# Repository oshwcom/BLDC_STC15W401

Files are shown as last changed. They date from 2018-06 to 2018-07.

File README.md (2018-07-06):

BLDC_STC15W401AS
===========================
一个低成本的12V无刷直流（BLDC）电机的驱动模块。

------

|Author|刘焕银|
|---|---
|E-mail|25199527@qq.com

------

## 目录
* [目标](#目标)
* [功能](#功能)
* [原理图](#原理图)

------

### 目标
    完成一款低成本（人民币7元以下）的BLDC驱动电路。  

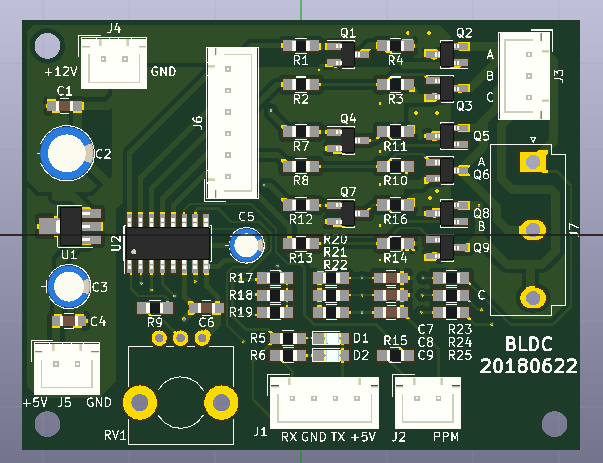
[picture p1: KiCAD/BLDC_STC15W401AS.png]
一款低成本BLDC驱动模块


------

### 功能
1. 驱动12V的BLDC电机，最大输出功率15瓦左右。
2. 可以正反转。
3. 转速800~1500转。

------

### 原理图
    V0.2版原理图。  修订了MOSFET的型号，多加了一种替代封装（SOT23和TO252)。

V0.2版原理图

------

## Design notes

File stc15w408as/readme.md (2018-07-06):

发行记录
===========================
该文件用来记录本次发行的问题

****
	
|Author|刘焕银|
|---|---
|E-mail|25199527@qq.com

已知Bug
------
### PMOS无法关断，换成NMOS后解决
    PMOS始终导通，上臂是12V，烧了大约30个下臂的NMOS。
### MOS管SOA控制不好
    下一版本，更换电流大一点的MOS管。

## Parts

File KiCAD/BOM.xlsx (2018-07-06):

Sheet: Sheet1
Id | 位号 | 封装 | 数量 | 描述
1 | J4 | JST_XH_B02B-XH-A_02x2.50mm_Straight | 1 | DC12V
2 | C1,C4,C6,C7,C8,C9 | C_0805_HandSoldering | 6 | 104
3 | C2 | CP_Radial_D6.3mm_P2.50mm | 1 | 470uF
4 | C3 | CP_Radial_D5.0mm_P2.00mm | 1 | 220uF
5 | C5 | CP_Radial_D4.0mm_P1.50mm | 1 | 47uF
6 | D1,D2 | LED_0805_HandSoldering | 2 | LED
7 | J1 | JST_XH_B04B-XH-A_04x2.50mm_Straight | 1 | Download
8 | J2 | JST_XH_B02B-XH-A_02x2.50mm_Straight | 1 | PPM
9 | J3 | JST_XH_B03B-XH-A_03x2.50mm_Straight | 1 | BLDC
10 | Q1,Q4,Q7 | SOT-23_Handsoldering | 3 | DTC143Z
11 | Q2,Q5,Q8 | SOT-23_Handsoldering | 3 | Q_PMOS_GSD
12 | Q3,Q6,Q9 | SOT-23_Handsoldering | 3 | Q_NMOS_GSD
13 | R1,R5,R6,R7,R12 | R_0805_HandSoldering | 5 | 1k
14 | R2,R8,R13 | R_0805_HandSoldering | 3 | 100
15 | R3,R10,R14 | R_0805_HandSoldering | 3 | 18K
16 | R4,R9,R11,R15,R16 | R_0805_HandSoldering | 5 | 470
17 | R17,R18,R19,R23,R24,R25 | R_0805_HandSoldering | 6 | 10k
18 | R20,R21,R22 | R_0805_HandSoldering | 3 | 2k
19 | RV1 | Potentiometer_Alps_RK09L_Sleve_Single_Horizontal | 1 | RK09L 10K
20 | U1 | SOT-89-3_Handsoldering | 1 | L78L05_SOT89
21 | U2 | SOIC-16_3.9x9.9mm_Pitch1.27mm | 1 | STC15W401AS-SOP16
22 | J5 | JST_XH_B02B-XH-A_02x2.50mm_Straight | 1 | DC5V
23 | J6 | JST_XH_B06B-XH-A_06x2.50mm_Straight | 1 | PWM
24 | J7 | JST_VH_B5P-VH-B_5A3x3.96mm_Vertical | 1 | BLDC

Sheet: Sheet2
Id | 位号 | 封装 | 数量 | 描述 | 单价 | 小计 | 本次数量
1 | J4 | JST_XH_B02B-XH-A_02x2.50mm_Straight | 1 | DC12V |  | 0 | 10
2 | C1,C4,C6,C7,C8,C9 | C_0805_HandSoldering | 6 | 104 |  | 0 | 60
3 | C2 | CP_Radial_D6.3mm_P2.50mm | 1 | 470uF |  | 0 | 10
4 | C3 | CP_Radial_D5.0mm_P2.00mm | 1 | 220uF |  | 0 | 10
5 | C5 | CP_Radial_D4.0mm_P1.50mm | 1 | 47uF |  | 0 | 10
6 | D1,D2 | LED_0805_HandSoldering | 2 | LED |  | 0
7 | J1 | JST_XH_B04B-XH-A_04x2.50mm_Straight | 1 | Download | 0 | 0 | 10
8 | J2 | JST_XH_B02B-XH-A_02x2.50mm_Straight | 1 | PPM | 0 | 0 | 10
9 | J3 | JST_XH_B03B-XH-A_03x2.50mm_Straight | 1 | BLDC | 0 | 0 | 10
10 | Q1,Q4,Q7 | SOT-23_Handsoldering | 3 | DTC143Z | 0.073 | 0.219 | 30
11 | Q2,Q5,Q8 | SOT-23_Handsoldering | 3 | Q_PMOS_GSD | 0.5 | 1.5 | 30
12 | Q3,Q6,Q9 | SOT-23_Handsoldering | 3 | Q_NMOS_GSD | 0.5 | 1.5 | 30
13 | R1,R5,R6,R7,R12 | R_0805_HandSoldering | 5 | 1k | 0.013 | 0.065 | 50
14 | R2,R8,R13 | R_0805_HandSoldering | 3 | 100 | 0.013 | 0.039 | 30
15 | R3,R10,R14 | R_0805_HandSoldering | 3 | 18K | 0.013 | 0.039 | 30
16 | R4,R9,R11,R15,R16 | R_0805_HandSoldering | 5 | 470 | 0.013 | 0.065 | 50
17 | R17,R18,R19,R23,R24,R25 | R_0805_HandSoldering | 6 | 10k | 0.013 | 0.078 | 60
18 | R20,R21,R22 | R_0805_HandSoldering | 3 | 2k | 0.013 | 0.039 | 30
19 | RV1 | Potentiometer_Alps_RK09L_Sleve_Single_Horizontal | 1 | RK09L 10K | 0 | 0 | 10
20 | U1 | SOT-89-3_Handsoldering | 1 | L78L05_SOT89 | 0.25 | 0.25 | 10
21 | U2 | SOIC-16_3.9x9.9mm_Pitch1.27mm | 1 | STC15W401AS-SOP16 | 2.2 | 2.2 | 10
22 | J5 | JST_XH_B02B-XH-A_02x2.50mm_Straight | 1 | DC5V | 0 | 0 | 10
23 | J6 | JST_XH_B06B-XH-A_06x2.50mm_Straight | 1 | PWM | 0 | 0 | 10
24 | J7 | JST_VH_B5P-VH-B_5A3x3.96mm_Vertical | 1 | BLDC | 0 | 0 | 10
 | PCB |  | 1 |  | 1.625 | 1.625 | 10
 | 制造包装测试费用 |  | 1 |  | 1.72 | 1.72
 |  |  |  |  | 总计： | 9.339
 | 电源，12V 3A | https://detail.1688.com/offer/565595260512.html?spm=a360q.7751291.0.0.579e3138QW1meo | 1 |  | 6.8 | 6.8
 | 电机， | https://detail.1688.com/offer/43696222362.html?spm=a360q.8274423.1130995625.41.49c84c9a2D6dGv | 1 |  | 13 | 13

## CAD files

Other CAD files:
stc15w408as/list/main-V20.obj
stc15w408as/comm.OBJ
doc/STC/STC15W401AS-实现四轴飞行器无刷电机的电调控制-参考程序和电路/list/main-V20.obj

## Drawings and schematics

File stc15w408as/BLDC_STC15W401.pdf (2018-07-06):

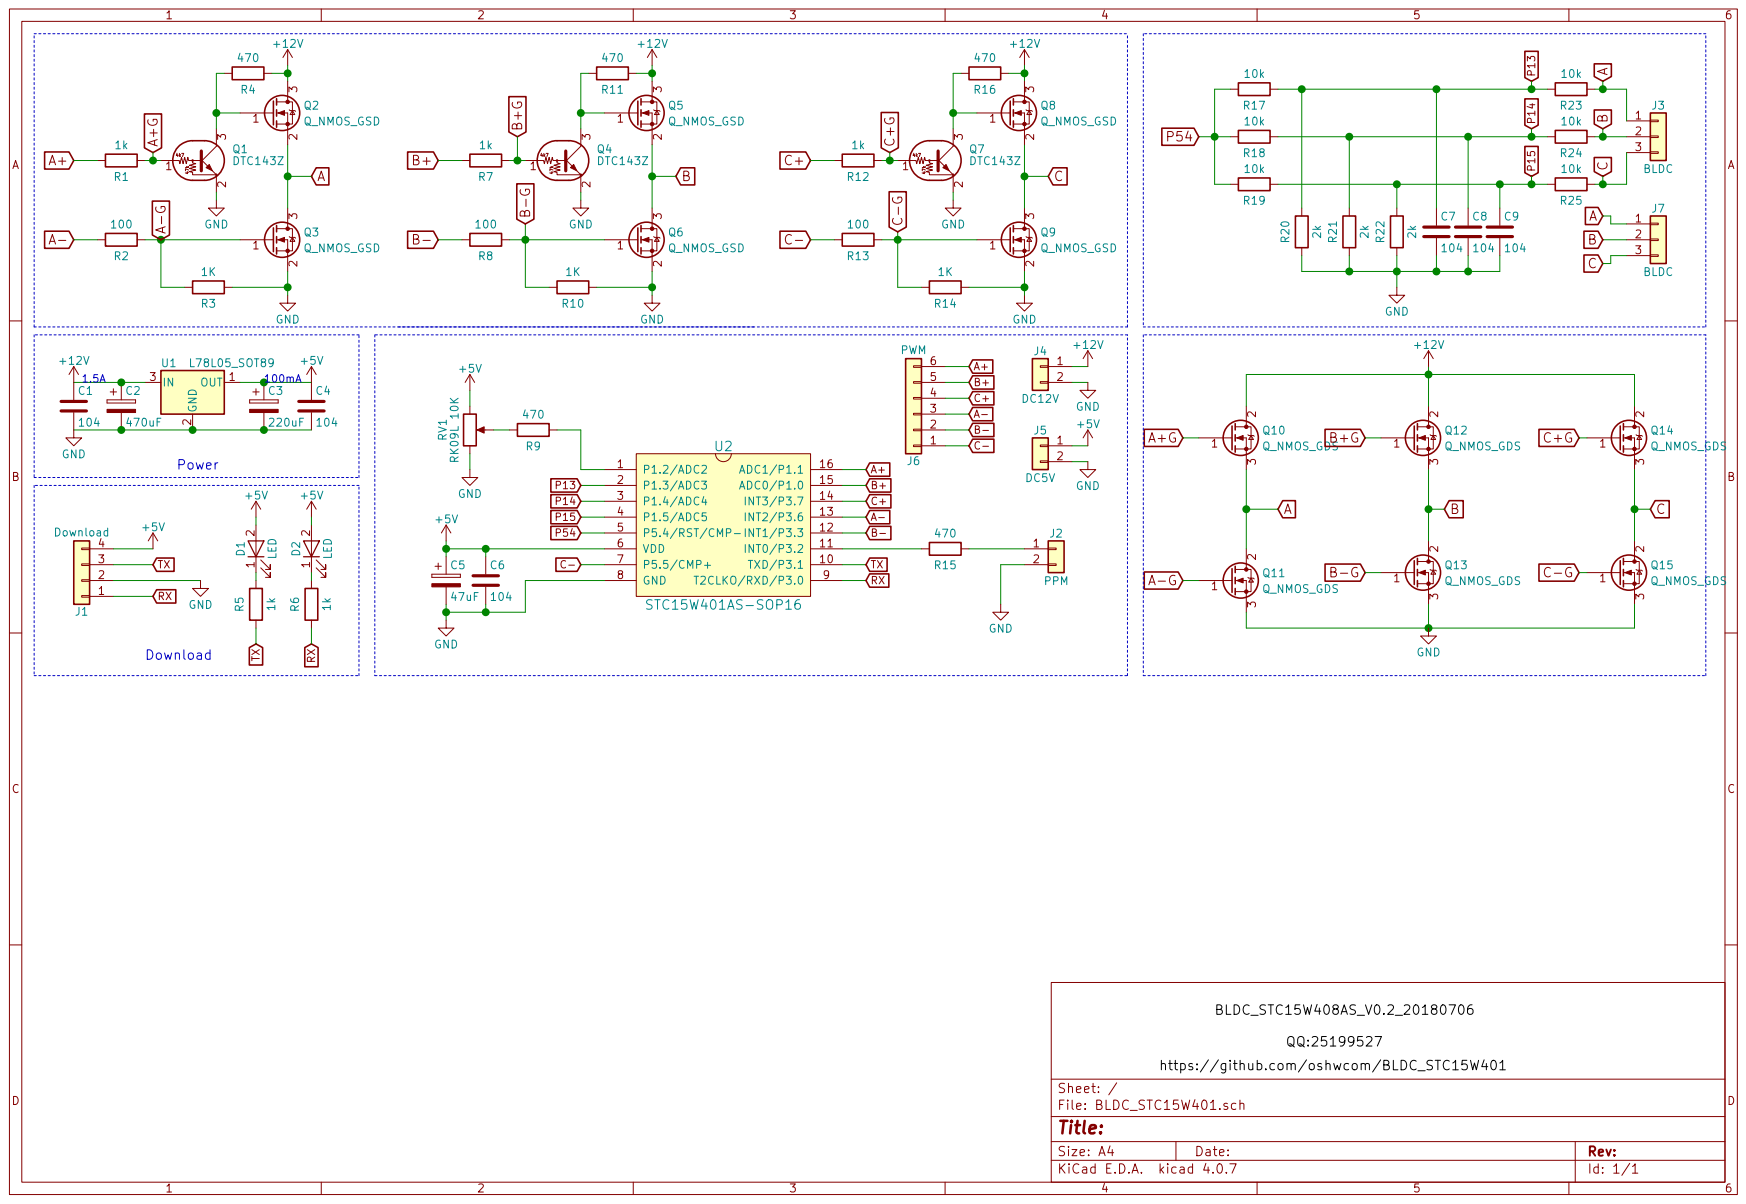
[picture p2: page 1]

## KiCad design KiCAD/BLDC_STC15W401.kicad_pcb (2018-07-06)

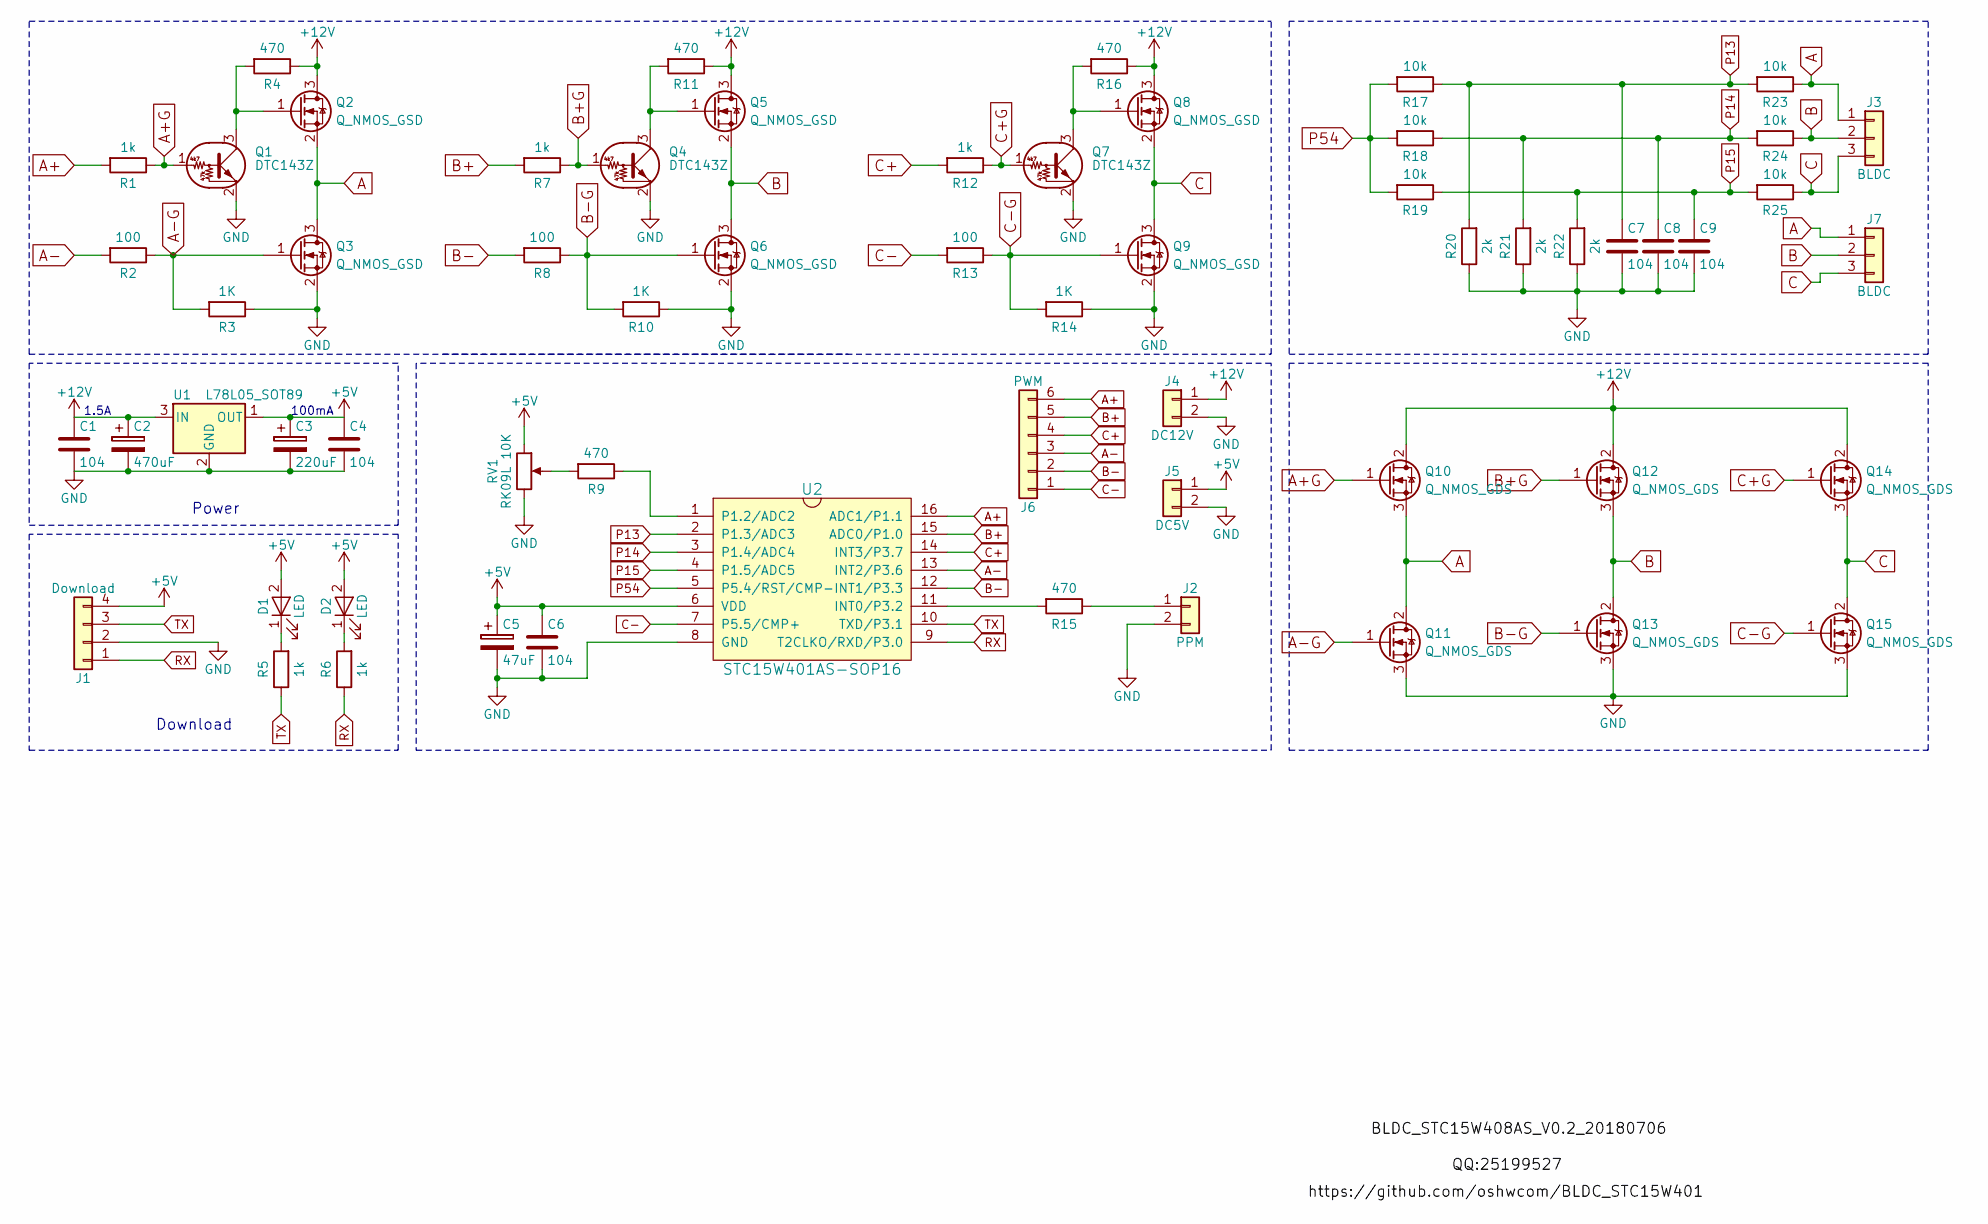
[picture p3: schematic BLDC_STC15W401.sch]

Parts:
C1, C4, C6, C7, C8, C9: 104; C_0805_HandSoldering
C2: 470uF; CP_Radial_D6.3mm_P2.50mm
C3: 220uF; CP_Radial_D5.0mm_P2.00mm
C5: 47uF; CP_Radial_D4.0mm_P1.50mm
D1, D2: LED; LED_0805_HandSoldering
J1: Download; JST_XH_B04B-XH-A_04x2.50mm_Straight
J2: PPM; JST_XH_B02B-XH-A_02x2.50mm_Straight
J3: BLDC; JST_XH_B03B-XH-A_03x2.50mm_Straight
J4: DC12V; JST_XH_B02B-XH-A_02x2.50mm_Straight
J5: DC5V; JST_XH_B02B-XH-A_02x2.50mm_Straight
J6: PWM; JST_XH_B06B-XH-A_06x2.50mm_Straight
J7: BLDC; JST_VH_B5P-VH-B_5A3x3.96mm_Vertical
Q1, Q4, Q7: DTC143Z; SOT-23_Handsoldering
Q2, Q3, Q5, Q6, Q8, Q9: Q_NMOS_GSD; SOT-23_Handsoldering
Q10, Q11, Q12, Q13, Q14, Q15: Q_NMOS_GDS; TO-252-2
R1, R5, R6, R7, R12: 1k; R_0805_HandSoldering
R2, R8, R13: 100; R_0805_HandSoldering
R3, R10, R14: 1K; R_0805_HandSoldering
R4, R9, R11, R15, R16: 470; R_0805_HandSoldering
R17, R18, R19, R23, R24, R25: 10k; R_0805_HandSoldering
R20, R21, R22: 2k; R_0805_HandSoldering
RV1: RK09L 10K; Potentiometer_Alps_RK09L_Sleve_Single_Horizontal
U1: L78L05_SOT89; SOT-89-3_Handsoldering
U2: STC15W401AS-SOP16; SOIC-16_3.9x9.9mm_Pitch1.27mm

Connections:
+5V: C3.1, C4.1, C5.1, C6.1, D1.2 (A), D2.2 (A), J1.4, J5.1, RV1.1, U1.1 (OUT), U2.6 (VDD)
+12V: C1.1, C2.1, J4.1, Q2.3 (D), Q5.3 (D), Q8.3 (D), Q10.2 (D), Q12.2 (D), Q14.2 (D), R4.1, R11.1, R16.1, U1.3 (IN)
A: J3.1, J7.1, Q2.2 (S), Q3.3 (D), Q10.3 (S), Q11.2 (D), R23.1
A+: J6.6, R1.2, U2.16 (ADC1/P1.1)
A+G: Q1.1 (B), Q10.1 (G), R1.1
A-: J6.3, R2.2, U2.13 (INT2/P3.6)
A-G: Q3.1 (G), Q11.1 (G), R2.1, R3.2
B: J3.2, J7.2, Q5.2 (S), Q6.3 (D), Q12.3 (S), Q13.2 (D), R24.1
B+: J6.5, R7.2, U2.15 (ADC0/P1.0)
B+G: Q4.1 (B), Q12.1 (G), R7.1
B-: J6.2, R8.2, U2.12 (INT1/P3.3)
B-G: Q6.1 (G), Q13.1 (G), R8.1, R10.2
C: J3.3, J7.3, Q8.2 (S), Q9.3 (D), Q14.3 (S), Q15.2 (D), R25.1
C+: J6.4, R12.2, U2.14 (INT3/P3.7)
C+G: Q7.1 (B), Q14.1 (G), R12.1
C-: J6.1, R13.2, U2.7 (P5.5/CMP+)
C-G: Q9.1 (G), Q15.1 (G), R13.1, R14.2
GND: C1.2, C2.2, C3.2, C4.2, C5.2, C6.2, C7.2, C8.2, C9.2, J1.2, J2.2, J4.2, J5.2, Q1.2 (E), Q3.2 (S), Q4.2 (E), Q6.2 (S), Q7.2 (E), Q9.2 (S), Q11.3 (S), Q13.3 (S), Q15.3 (S), R3.1, R10.1, R14.1, R20.1, R21.1, R22.1, RV1.3, U1.2 (GND), U2.8 (GND)
unnamed: D1.1 (K), R5.2
unnamed: D2.1 (K), R6.2
unnamed: J2.1, R15.1
unnamed: Q1.3 (C), Q2.1 (G), R4.2
unnamed: Q4.3 (C), Q5.1 (G), R11.2
unnamed: Q7.3 (C), Q8.1 (G), R16.2
unnamed: R9.1, U2.1 (P1.2/ADC2)
unnamed: R9.2, RV1.2
unnamed: R15.2, U2.11 (INT0/P3.2)
P13: C7.1, R17.1, R20.2, R23.2, U2.2 (P1.3/ADC3)
P14: C8.1, R18.1, R21.2, R24.2, U2.3 (P1.4/ADC4)
P15: C9.1, R19.1, R22.2, R25.2, U2.4 (P1.5/ADC5)
P54: R17.2, R18.2, R19.2, U2.5 (P5.4/RST/CMP-)
RX: J1.1, R6.1, U2.9 (T2CLKO/RXD/P3.0)
TX: J1.3, R5.1, U2.10 (TXD/P3.1)

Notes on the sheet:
Power
Download
100mA
1.5A

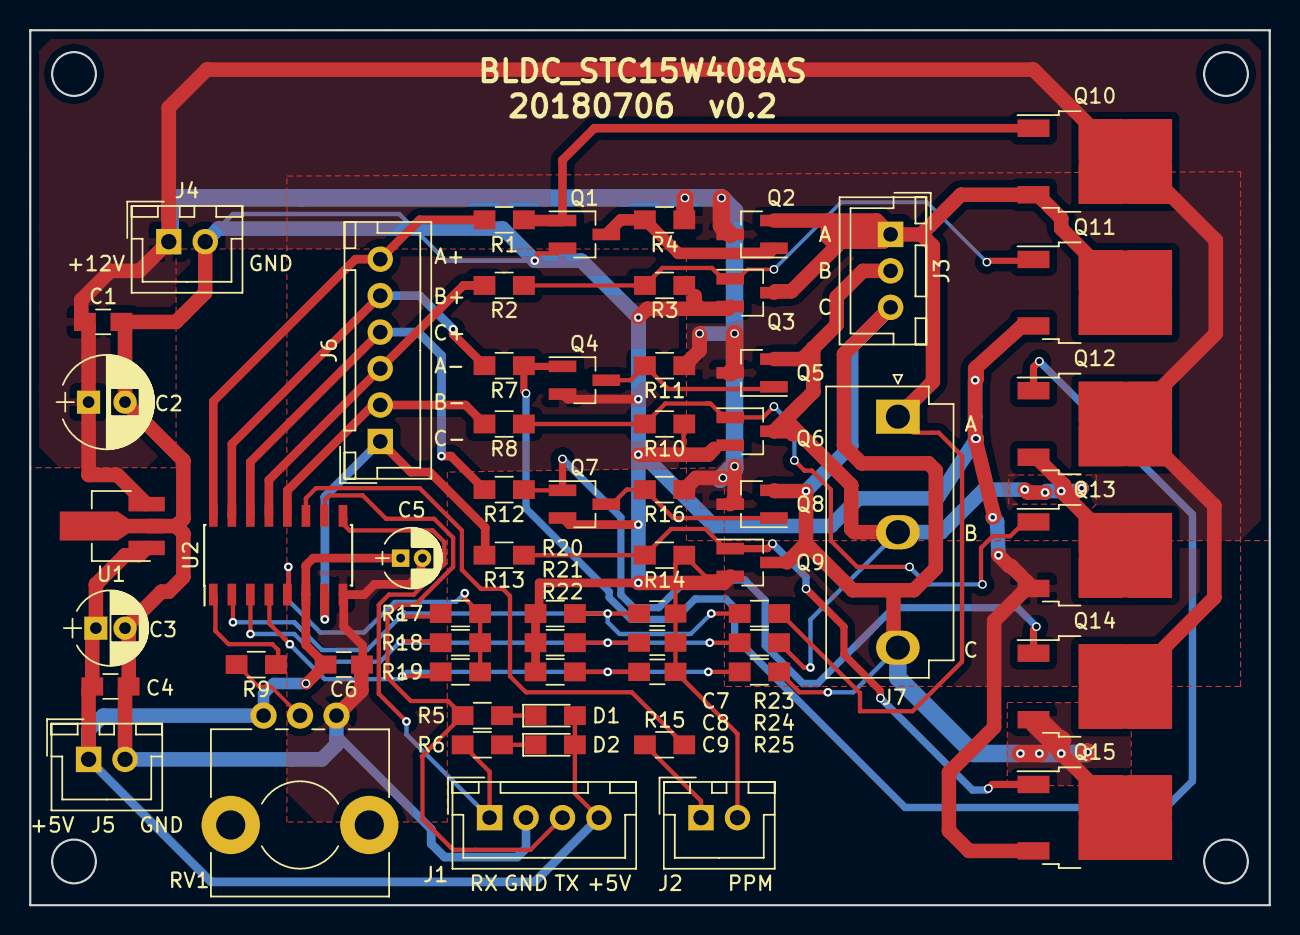
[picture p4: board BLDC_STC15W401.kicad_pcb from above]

Board: 2 copper layers, 85.0 x 60.0 mm, 61 parts (0 on the bottom side), 33 nets.

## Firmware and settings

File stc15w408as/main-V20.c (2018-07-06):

/*---------------------------------------------------------------------*/
/* --- STC MCU International Limited ----------------------------------*/
/* --- STC 1T Series MCU Demo Programme -------------------------------*/
/* --- Mobile: 13922805190 --------------------------------------------*/
/* --- Fax: 0513-55012956,55012947,55012969 ---------------------------*/
/* --- Tel: 0513-55012928,55012929,55012966 ---------------------------*/
/* --- Web: www.GXWMCU.com   www.stcmcu.com ---------------------------*/
/* --- QQ:  800003751 -------------------------------------------------*/
/* 如果要在程序中使用此代码,请在程序中注明使用了宏晶科技的资料及程序   */
/*---------------------------------------------------------------------*/


/*************	功能说明	**************

本程序试验使用STC15W401AS-35I-SOP16<RMB1.6>来驱动航模用的无传感器无刷三相直流马达.

本程序参考自网上的代码(作者: 瑞生), 改良而来.

电路图见文件 "BLDC-V10-实验电路.pdf".

控制信号由P3.2输入正脉冲信号, 间隔5~20ms, 脉冲宽度1.000~1.610ms.

1.160ms开始启动, 1.610ms为最高速度, 分辨率为2us.

本程序仅仅是简单控制, 软件没有处理 过0延时30度切换 过流检测.

由于过0检测部分有RC滤波, 所以改变电容值可以大约的对应在最高速时延时30度的时间.

有意者可自行完善电路和程序.

******************************************/




#define MAIN_Fosc		24000000L	//定义主时钟

#include "STC15Fxxxx.H"

#define		MCU_PIN		16	/* 选择MCU引脚数, 只支持16或20脚(28脚或32脚跟20脚一样) */

// #include "reg51.h"
#include "intrins.h"

typedef unsigned char BYTE;
typedef unsigned int WORD;
void SendData(BYTE dat);
void SendString(char *s);
// #define FOSC 11059200L          //系统频率
// #define BAUD 115200             //串口波特率

#define NONE_PARITY     0       //无校验
#define ODD_PARITY      1       //奇校验
#define EVEN_PARITY     2       //偶校验
#define MARK_PARITY     3       //标记校验
#define SPACE_PARITY    4       //空白校验

#define PARITYBIT NONE_PARITY   //定义校验位



//CMPCR1
#define	CMPEN	0x80	//1: 允许比较器, 0: 禁止,关闭比较器电源
#define	CMPIF	0x40	//比较器中断标志, 包括上升沿或下降沿中断, 软件清0
#define	PIE		0x20	//1: 比较结果由0变1, 产生上升沿中断
#define	NIE		0x10	//1: 比较结果由1变0, 产生下降沿中断
#define	PIS		0x08	//输入正极性选择, 0: 选择外部P5.5做正输入,           1: 由ADCIS[2:0]所选择的ADC输入端做正输入.
#define	NIS		0x04	//输入负极性选择, 0: 选择内部BandGap电压BGv做负输入, 1: 选择外部P5.4做输入.
#define	CMPOE	0x02	//1: 允许比较结果输出到P1.2, 0: 禁止.
#define	CMPRES	0x01	//比较结果, 1: CMP+电平高于CMP-,  0: CMP+电平低于CMP-,  只读

//CMPCR2
#define	INVCMPO	0x80	//1: 比较器输出取反,  0: 不取反
#define	DISFLT	0x40	//1: 关闭0.1uF滤波,   0: 允许
#define	LCDTY	0x00	//0~63, 比较结果变化延时周期数

#if	(MCU_PIN == 20)
	sbit PWM2_L = P3^4;
	sbit PWM1_L = P3^5;
	sbit PWM0_L = P3^6;
#endif

#if	(MCU_PIN == 16)
	sbit PWM2_L = P5^5;		// C-
	sbit PWM1_L = P3^3;		// B-
	sbit PWM0_L = P3^6;		// A-
#endif

u8	Step;
u8	PWM_Value; // 决定PWM占空比的值
u16	RxPulseWide;
bit	B_RxOk;
bit	B_RUN;
u8	PWW_Set;
u8	cnt10ms;
u8	Rx_cnt;
u8	TimeOut;	//堵转超时

#define DISABLE_CMP_INT CMPCR1 &= ~0X40		// 关闭比较器中断
#define ENABLE_CMP_INT  CMPCR1 |= 0X40		// 打开比较器中断

/*************************/

void	Delay_n_ms(u8 dly)
{
	u16	j;
	do
	{
		j = MAIN_Fosc / 13000;	//延时1ms, 主程序在此节拍下运行
		while(--j)	;
	}while(--dly);
}


void delay_us(u8 us)
{
	do
	{
		NOP(20);	//@24MHz
	}
	while(--us);
}

void StepXL(void) // 换相序列函数
{
 switch(Step)
  {
   case 0:  // AB
			PWM0_L=0;	PWM2_L=0;
			PWM0_OUT_1();
			PWM1_OUT_1();
			PWM2_OUT_1();
			PWM0_NORMAL();
			CCAP0H = PWM_Value;		// 打开A相的高端
			PWM1_L = 1; 		// 打开B相的低端
			ADC_CONTR = 0XED;	// 选择P1.5作为ADC输入 即c相电压
			CMPCR1 = 0x9C;		//bit7=1 允许比较器, bit4=1 比较结果由1变0, 产生下降沿中断 (不能响应下降沿中断?)
		break;
   case 1:  // AC
			PWM0_L=0;	PWM1_L=0;
			PWM0_OUT_1();
			PWM1_OUT_1();
			PWM2_OUT_1();
			PWM0_NORMAL();
			CCAP0H = PWM_Value;		// 打开A相的高端
			PWM2_L = 1;			// 打开C相的低端
			ADC_CONTR = 0XEC;	// 选择P1.4作为ADC输入 即B相电压
			CMPCR1 = 0xAC;		//上升沿中断
	 
      	break;
   case 2:  // BC
			PWM0_L=0;	PWM1_L=0;
			PWM0_OUT_1();
			PWM1_OUT_1();
			PWM2_OUT_1();
			PWM1_NORMAL();
			CCAP1H = PWM_Value; // 打开B相的高端
			PWM2_L = 1;			// 打开C相的低端
			ADC_CONTR = 0XEB;	// 选择P1.3作为ADC输入 即a相电压
			CMPCR1 = 0x9C;		//下降沿中断
      	break;
   case 3:  // BA
			PWM1_L=0;	PWM2_L=0;
			PWM0_OUT_1();
			PWM1_OUT_1();
			PWM2_OUT_1();
			PWM1_NORMAL();
			CCAP1H = PWM_Value; // 打开B相的高端
			PWM0_L = 1;			// 打开A相的低端
			ADC_CONTR = 0XED;	// 选择P1.5作为ADC输入 即c相电压 
			CMPCR1 = 0xAC;		//上升沿中断
			
      	break;
   case 4: // CA
			PWM1_L=0;	PWM2_L=0;
			PWM0_OUT_1();
			PWM1_OUT_1();
			PWM2_OUT_1();
			PWM2_NORMAL();
			CCAP2H = PWM_Value; // 打开C相的高端
			PWM0_L = 1;			// 打开A相的低端
			ADC_CONTR = 0XEC;	// 选择P1.4作为ADC输入 即B相电压
			CMPCR1 = 0x9C;		//下降沿中断
     	break;
   case 5: // CB
      		PWM0_L=0;	PWM2_L=0;
			PWM0_OUT_1();
			PWM1_OUT_1();
			PWM2_OUT_1();
			PWM2_NORMAL();
			CCAP2H = PWM_Value; // 打开C相的高端
      		PWM1_L = 1;			// 打开B相的低端
			ADC_CONTR = 0XEB;	// 选择P1.3作为ADC输入 即a相电压
			CMPCR1 = 0xAC;		//上升沿中断
	 
		break;
	 
	default:
		break;
  }	
}



void PWM_Init(void)
{
	PWM0_L = 0;
	PWM1_L = 0;
	PWM2_L = 0;
	
	#if	(MCU_PIN == 20)
		P3n_push_pull(0x70);
	#endif
	#if	(MCU_PIN == 16)
		P3n_push_pull(0x48);
		P5n_push_pull(0x20);
	#endif

	// CMOD = 1 << 1; //选择系统时钟/2为时钟源，即PWM频率=24M/2/256=46.9K
	CMOD = 5 << 1; //选择系统时钟/4为时钟源，即PWM频率=24M/4/256=23.4K
	// CMOD = 6 << 1; //选择系统时钟/6为时钟源，即PWM频率=24M/6/256=15.6K
	CL=0;			// PCA计数器清零
	CH=0;
	
	PCA_PWM0 = 0X00;
	CCAP0H=0;    // 初始化占空比为0% H的值装载到L中
	CCAP0L=0;
	CCAPM0=0x42;	// 设置为PWM模式, 8位，无中断。

	PCA_PWM1 = 0X00;
	CCAP1H=0;    // 初始化占空比为0%
	CCAP1L=0;
	CCAPM1=0x42;	// 设置为PWM模式
	
	PCA_PWM2 = 0X00;
	CCAP2H=0;    // 初始化占空比为0%
	CCAP2L=0;
	CCAPM2=0x42;	// 设置为PWM模式
	
	PWM0_OUT_1();
	PWM1_OUT_1();
	PWM2_OUT_1();

	CR = 1;
}

void ADC_Init(void)
{
	P1n_pure_input(0x38);
	P1ASF = 0X38; // 开通P1.3 P1.4 P1.5的AD输入口
}

void CMP_INT(void) interrupt 21
{
	CMPCR1 &= ~0X40; // 需软件清除中断标志位
	if(Step<5)	Step++;
	else		Step = 0;
	StepXL();
	TimeOut = 10;	//10ms超时
}

void CMP_Init(void)
{
	CMPCR1 = 0X8C;	// 1000 1100 打开比较器，P5.4作为比较器的反相输入端，ADC引脚作为正输入端 
	CMPCR2 = 60;	// 60个时钟滤波
	P5n_pure_input(0x10);
}

u8 StartMotor(void)
{
	u16 timer,i;
	DISABLE_CMP_INT;	// 禁止比较器中断
	PWM_Value = 30;		// 初始占空比=16/256=6%
	Step = 0;
	StepXL();			// 初始位置
	Delay_n_ms(5);//delay_ms(5);
	timer = 300;

	while(1)
	{
		for(i=0; i<timer; i++)	delay_us(50);  // 第一次是15毫秒，加上上面的5毫米延时，总计大约20毫秒
		timer -= timer /15 + 1;
		if(timer < 25)	{
			CMPCR1 &= ~0X40; 	// 需软件清除中断标志位
			B_RUN = 1;			// 马达运行标志位
			PWM_Value = 0;		// 启动完成。停转，等串口的PWW_SET值
			TimeOut = 10;		// 10毫米超时
			ENABLE_CMP_INT; 	// 打开比较器中断
			return(1);
		}
		if( Step < 5)	Step++;
		else			Step = 0;
		StepXL();
		// SendString("Start Motor!\r\n");
	}
}

// void T0_Iint(void)
// {
// 	Timer0_AsTimer();	/* 时器0用做定时器	*/
// 	Timer0_12T();		/* Timer0 clodk = fo/12	12分频,	default	*/
// 	Timer0_16bit();
// 	Timer0_Gate_INT0_P32();	/* 时器0由外部INT0高电平允许定时计数 */
// 	TH0 = 0;
// 	TL0 = 0;
// 	TR0 = 1; // 打开定时器0
// 	ET0 = 1;// 允许ET0中断
// }

// void T0_Interrupt(void) interrupt 1
// {
// 	Rx_cnt = 0;			//一旦出现溢出, 则开始的n个脉冲无效
// 	RxPulseWide = 1000;	//停止
// 	B_RxOk = 1;			//虚拟收到一个脉冲
// }

/********************* INT0中断函数 *************************/
// void INT0_int (void) interrupt INT0_VECTOR
// {
// 	u16	j;
	
// 	TR0 = 0;
// 	j = ((u16)TH0 << 8) + TL0;
// 	TH0 = 0;
// 	TL0 = 0;
// 	TR0 = 1;

// 	if(++Rx_cnt >= 5)	Rx_cnt = 5;
// 	j >>= 1;	//为了好处理, 转成单位为us
// 	if((j >= 800) && (j <= 2000) && (Rx_cnt == 5))
// 	{
// 		RxPulseWide = j;
// 		B_RxOk = 1;		//标志收到一个脉冲
// 	}

// }

/********************* 串口初始化函数 *************************/
bit busy;


void UartInit(void)		//9600bps@24.000MHz
{
	SCON = 0x50;		//8位数据,可变波特率
	AUXR |= 0x01;		//串口1选择定时器2为波特率发生器
	AUXR |= 0x04;		//定时器2时钟为Fosc,即1T
	T2L = 0x8F;		//设定定时初值
	T2H = 0xFD;		//设定定时初值
	AUXR |= 0x10;		//启动定时器2
    ES = 1;                     //使能串口1中断
}


/*----------------------------
UART 中断服务程序
-----------------------------*/
void Uart() interrupt 4 using 1
{
    ES = 0;         //关闭串口中断
	if (RI)
    {
		PWW_Set = SBUF; // 把收到的数据给了PWW_Set
		RI=0; // 串口接收标志清0
		B_RxOk = 1;
    }
    if (TI)
    {
        TI = 0;                 //清除TI位
        busy = 0;               //清忙标志
    }
	ES = 1;         //使能串口中断
}


/*----------------------------
发送串口数据
----------------------------*/
void SendData(BYTE dat)
{
    while (busy);               //等待前面的数据发送完成
    ACC = dat;                  //获取校验位P (PSW.0)
    if (P)                      //根据P来设置校验位
    {
		#if (PARITYBIT == ODD_PARITY)
				TB8 = 0;                //设置校验位为0
		#elif (PARITYBIT == EVEN_PARITY)
				TB8 = 1;                //设置校验位为1
		#endif
    }
    else
    {
		#if (PARITYBIT == ODD_PARITY)
				TB8 = 1;                //设置校验位为1
		#elif (PARITYBIT == EVEN_PARITY)
				TB8 = 0;                //设置校验位为0
		#endif
    }
    busy = 1;
    SBUF = ACC;                 //写数据到UART数据寄存器
}

/*----------------------------
发送字符串
----------------------------*/
void SendString(char *s)
{
    while (*s)                  //检测字符串结束标志
    {
        SendData(*s++);         //发送当前字符
    }
}


/**********************************************/

void main(void)
{
	PWM_Init();
	ADC_Init();
	CMP_Init();
	UartInit();
	// T0_Iint();

	IE0 = 0;	// 清除外中断0标志位
	// EX0 = 1;	// INT0 Enable
	// IT0 = 1;	//INT0 下降沿中断
	
	// RxPulseWide = 1000;
	PWW_Set = 0;
	cnt10ms = 0;
	Rx_cnt  = 0;
	TimeOut = 0;

	EA = 1; // 打开总中断
	// Delay_n_ms(1);	//延时
	SendString("BLDC Test !\r\n");
	while (1)
	{
		Delay_n_ms(1);	//延时1ms, 主程序在此节拍下运行

		if (TimeOut > 0)
		{
			if(--TimeOut == 0)	//堵转超时
			{
				DISABLE_CMP_INT; 	// 关比较器中断
				CCAP0H=0;	CCAP1H=0;	CCAP2H=0;  // 占空比为0
				PWM0_L=0;	PWM1_L=0;	PWM2_L=0;
				// RxPulseWide = 1000;
				PWW_Set   = 0;
				PWM_Value = 0;
				B_RxOk = 0;
				B_RUN  = 0;
				Rx_cnt = 0;
				TimeOut = 0;
				SendString("Time Out!\r\n");

				Delay_n_ms(250);	//堵转时,延时1秒再启动
				Delay_n_ms(250);
				Delay_n_ms(250);
				Delay_n_ms(250);

			}
		}
		
		// if(B_RxOk)	//收到一个脉冲
		// {
		// 	B_RxOk = 0;
		// 	j = RxPulseWide;
		// 	if(j >= 1100)				// 1100~1610对应PWM占空比值0~255
		// 	{
		// 		j = (j - 1100) >> 1;	//2us对应PWM一个步进
		// 		if(j > 256)	j = 255;
		// 	}
		// 	else	j = 0;
		// 	PWW_Set = (u8)j;
		// }
		// SendData(PWW_Set);
		if(B_RxOk) // 如果串口收到数据
		{
			// SendData(PWW_Set);
			B_RxOk = 0;
			// if(rec==0x22)// 加速命令
			// {
			// 	if(PWM_Value<250)
			// 	{
			// 		PWM_Value++; // 增加占空比
			// 	}
			// }
			// else if(rec==0x33)// 减速命令
			// {
			// 	if(PWM_Value>30)
			// 	{
			// 		PWM_Value--; // 减小占空比
			// 	}
			// }
			// else if(rec==0x11) // 启动命令
			// {
			// 	StartMotor();	// 启动马达
			// 	CMPCR1 &= ~0X40; // 需软件清除中断标志位
			// 	ENABLE_CMP_INT; // 打开比较器中断
			// 	B_RUN = 1;
			// 	TimeOut = 0;
			// }
			// else if(rec==0x44) // 停止命令
			// {
			// 	CCAP0H=0;CCAP1H=0;CCAP2H=0;  // 占空比都置0
			// 	EA = 0; // 关闭全局中断
			// 	DISABLE_CMP_INT; // 关闭比较器中断
			// }
		}
		if(!B_RUN && (PWW_Set >= 30))		// PWM_Set >= 30, 并且马达未运行, 则启动马达
		{
			StartMotor();	// 启动马达
			// TimeOut = 0;
		}
		
		
		if(++cnt10ms >= 10)		// 10ms时隙
		{
			// SendData(cnt10ms);
			cnt10ms = 0;
			if(B_RUN)
			{
				if(PWM_Value < PWW_Set)	PWM_Value++;
				if(PWM_Value > PWW_Set)	PWM_Value--;
				if(PWM_Value < 20)	// 停转
				{
					PWM_Value = 0;
					B_RUN = 0;
					CCAP0H=0;	CCAP1H=0;	CCAP2H=0;  // 占空比为0
					PWM0_L=0;	PWM1_L=0;	PWM2_L=0;
					DISABLE_CMP_INT; // 关比较器中断
					SendString("Stop Motor!\r\n");
				}
			}
		}
	}
}

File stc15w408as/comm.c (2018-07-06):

/*---------------------------------------------------------------------*/
/* --- STC MCU Limited ------------------------------------------------*/
/* --- STC15F4K60S4 系列 定时器2用作串口1的波特率发生器举例------------*/
/* --- Mobile: (86)13922805190 ----------------------------------------*/
/* --- Fax: 86-0513-55012956,55012947,55012969 ------------------------*/
/* --- Tel: 86-0513-55012928,55012929,55012966-------------------------*/
/* --- Web: www.STCMCU.com --------------------------------------------*/
/* --- Web: www.GXWMCU.com --------------------------------------------*/
/* 如果要在程序中使用此代码,请在程序中注明使用了STC的资料及程序        */
/* 如果要在文章中应用此代码,请在文章中注明使用了STC的资料及程序        */
/*---------------------------------------------------------------------*/

//本示例在Keil开发环境下请选择Intel的8058芯片型号进行编译
//若无特别说明,工作频率一般为11.0592MHz


#include "reg51.h"
#include "intrins.h"

typedef unsigned char BYTE;
typedef unsigned int WORD;

#define FOSC 11059200L          //系统频率
#define BAUD 115200             //串口波特率

#define NONE_PARITY     0       //无校验
#define ODD_PARITY      1       //奇校验
#define EVEN_PARITY     2       //偶校验
#define MARK_PARITY     3       //标记校验
#define SPACE_PARITY    4       //空白校验

#define PARITYBIT EVEN_PARITY   //定义校验位

sfr P0M1 = 0x93;
sfr P0M0 = 0x94;
sfr P1M1 = 0x91;
sfr P1M0 = 0x92;
sfr P2M1 = 0x95;
sfr P2M0 = 0x96;
sfr P3M1 = 0xb1;
sfr P3M0 = 0xb2;
sfr P4M1 = 0xb3;
sfr P4M0 = 0xb4;
sfr P5M1 = 0xC9;
sfr P5M0 = 0xCA;
sfr P6M1 = 0xCB;
sfr P6M0 = 0xCC;
sfr P7M1 = 0xE1;
sfr P7M0 = 0xE2;

sfr AUXR  = 0x8e;               //辅助寄存器
sfr T2H   = 0xd6;               //定时器2高8位
sfr T2L   = 0xd7;               //定时器2低8位

sfr P_SW1   = 0xA2;             //外设功能切换寄存器1

#define S1_S0 0x40              //P_SW1.6
#define S1_S1 0x80              //P_SW1.7

sbit P22 = P2^2;

bit busy;

void SendData(BYTE dat);
void SendString(char *s);

void main()
{
    P0M0 = 0x00;
    P0M1 = 0x00;
    P1M0 = 0x00;
    P1M1 = 0x00;
    P2M0 = 0x00;
    P2M1 = 0x00;
    P3M0 = 0x00;
    P3M1 = 0x00;
    P4M0 = 0x00;
    P4M1 = 0x00;
    P5M0 = 0x00;
    P5M1 = 0x00;
    P6M0 = 0x00;
    P6M1 = 0x00;
    P7M0 = 0x00;
    P7M1 = 0x00;

    ACC = P_SW1;
    ACC &= ~(S1_S0 | S1_S1);    //S1_S0=0 S1_S1=0
    P_SW1 = ACC;                //(P3.0/RxD, P3.1/TxD)
    
    //  ACC = P_SW1;
    //  ACC &= ~(S1_S0 | S1_S1);    //S1_S0=1 S1_S1=0
    //  ACC |= S1_S0;               //(P3.6/RxD_2, P3.7/TxD_2)
    //  P_SW1 = ACC;  
    //  
    //  ACC = P_SW1;
    //  ACC &= ~(S1_S0 | S1_S1);    //S1_S0=0 S1_S1=1
    //  ACC |= S1_S1;               //(P1.6/RxD_3, P1.7/TxD_3)
    //  P_SW1 = ACC;  

    #if (PARITYBIT == NONE_PARITY)
        SCON = 0x50;                //8位可变波特率
    #elif (PARITYBIT == ODD_PARITY) || (PARITYBIT == EVEN_PARITY) || (PARITYBIT == MARK_PARITY)
        SCON = 0xda;                //9位可变波特率,校验位初始为1
    #elif (PARITYBIT == SPACE_PARITY)
        SCON = 0xd2;                //9位可变波特率,校验位初始为0
    #endif

    T2L = (65536 - (FOSC/4/BAUD));   //设置波特率重装值
    T2H = (65536 - (FOSC/4/BAUD))>>8;
    AUXR = 0x14;                //T2为1T模式, 并启动定时器2
    AUXR |= 0x01;               //选择定时器2为串口1的波特率发生器
    ES = 1;                     //使能串口1中断
    EA = 1;

    SendString("STC15F2K60S2\r\nUart Test !\r\n");
    while(1);
}

/*----------------------------
UART 中断服务程序
-----------------------------*/
void Uart() interrupt 4 using 1
{
    if (RI)
    {
        RI = 0;                 //清除RI位
        P0 = SBUF;              //P0显示串口数据
        P22 = RB8;              //P2.2显示校验位
    }
    if (TI)
    {
        TI = 0;                 //清除TI位
        busy = 0;               //清忙标志
    }
}

/*----------------------------
发送串口数据
----------------------------*/
void SendData(BYTE dat)
{
    while (busy);               //等待前面的数据发送完成
    ACC = dat;                  //获取校验位P (PSW.0)
    if (P)                      //根据P来设置校验位
    {
#if (PARITYBIT == ODD_PARITY)
        TB8 = 0;                //设置校验位为0
#elif (PARITYBIT == EVEN_PARITY)
        TB8 = 1;                //设置校验位为1
#endif
    }
    else
    {
#if (PARITYBIT == ODD_PARITY)
        TB8 = 1;                //设置校验位为1
#elif (PARITYBIT == EVEN_PARITY)
        TB8 = 0;                //设置校验位为0
#endif
    }
    busy = 1;
    SBUF = ACC;                 //写数据到UART数据寄存器
}

/*----------------------------
发送字符串
----------------------------*/
void SendString(char *s)
{
    while (*s)                  //检测字符串结束标志
    {
        SendData(*s++);         //发送当前字符
    }
}

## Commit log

2018-06-23 首次提交
    [BLDC_STC15W401-B.Cu.gbl, BLDC_STC15W401-B.Mask.gbs, BLDC_STC15W401-Edge.Cuts.gm1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]
2018-06-23 添加readme.txt和.gitignore文件
2018-06-23 Update readme.txt
    更改文件格式
2018-06-23 更新Readme。 更改报价资料
    [BLDC_STC15W401.xls]
2018-06-23 增加说明文件
2018-06-23 更新说明文件
2018-06-23 删除多余文件
2018-06-23 更新描述文件
2018-06-23 添加产品图片
2018-07-06 添加BOM及N多MOSFET的datasheet
    [BLDC_STC15W401.xls, BOM.xlsx]
2018-07-06 添加V0.2的PCB设计
    [BLDC_STC15W401-B.Cu.gbl, BLDC_STC15W401-B.Mask.gbs, BLDC_STC15W401-Edge.Cuts.gm1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]
2018-07-06 添加软件代码，从飞控的PPM改成串口调速。
    [comm.OBJ, main-V20.obj]
2018-07-06 添加原理图
2018-07-06 添加SVG格式原理图
2018-07-06 更新说明文档
